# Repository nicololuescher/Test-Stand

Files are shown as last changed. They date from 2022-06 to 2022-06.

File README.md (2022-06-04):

# Modular Test Stand

## What is this?
This is a simple and modular test rig to test hobby rocket motors. It is especially useful to measure homemade rocket motors and check their specs. It is constructed with a modular design in mind. This means that it can simply be converted to measure other forces for other tests.  
I'm neither a Physicist nor a Mechanical Engineer. I'm a Software Engineer. So take this with a grain of salt and feel free to make changes if necesarry.  
  
I just wanted to share my work in hopes that others may find it useful.

## Materials Needed (for my setup)
- ESP32 Microprocessor (NODEESP in my case)
- CZL601 (I have the 50kg version https://www.tinkerforge.com/en/shop/load-cell-50kg-czl601.html)
- HX711 Load Cell Amplifier (https://www.bastelgarage.ch/load-cell-amplifier-hx711-wiegesensor-24-bit)
- Soldering Iron and Jumper Cables
- A USB powerbank
- About 50cm of 20x20mm Aluminium Strut Profile
- 10x M5 T Nut for 20x20mm Strut Profile
- 10x M5x16mm Bolt
- 10x M5 Washer
- 2x M6x30mm Bolt
- 2x M6 Washer
- A 3D Printer
- Basic CAD Knwoledge to create Custom Adapters
- A Server running a MQTT Broker (Mosquitto)

## Prerequisite
You will need a MQTT Broker. [This](https://www.digitalocean.com/community/tutorials/how-to-install-and-secure-the-mosquitto-mqtt-messaging-broker-on-ubuntu-16-04) tutorial from DigitalOcean shows you how you can set up such a service.

## How to build
1. Connect the Load Cell and the Load Cell Amplifier according to the wiring diagram below. (GND - GND, DT - GPIO 16, SCK - GPIO 4, VCC - VCC, Red - E+, Yellow - E-, Black and White - A-, Blue - A+)
wiring

1. Cut 2 pieces from your aluminium extrusion. One about 25cm (lower Structure) and the second about 12cm (upper arm).

1. Print the STL files.

1. Assemble the Scale according to the picture .
scale
esp_container

1. Secure the electronics with cable ties

1. Follow the "Calibrate the Scale" Step in [this](https://randomnerdtutorials.com/esp32-load-cell-hx711/#calibrate-load-cell) tutorial to get the calibration factor

1. Open up the teststand.ino file and fill in your information including the calibration factor in the scale.set_scale(factor). Upload the programm to your ESP32. I recommend you use a mobile hotspot for your wifi connection. This way you are not constrained by your local WIFI.

1. Open up index.html in your Webbrowser of choice (tested in Chrome) and connect your USB Powerbank to the ESP32.

1. Wait until the Scale connectos to the Webinterface.

1. If you see the Connected! prompt in your JS Console and you see data comming in, you are all set.

## How to use the Interface
webinterface
### Enable Graph
This checkbox toggles the Diagram

### Pause / Resume
This button pauses/resumes the datalogging.

### Reset
Clears the ouput. This has no effect on calibration.

### Zero
Zero the scale. E.g. takes the current reading as an offset.

### Tare
To be used in conjunction with Calibrate. Sets the empty weight of the scale. Remove everything on the scale and click "Tare" to start the calibration.

### Calibrate
You have to Tare the scale first. After that, set a known weight on the scale. Put the weight of the object in grams in the input field and click Calibrate. This is useful for when you exchange adapters so you dont have to re-calculate the calibration factor.

### Export Data
This will create a JSON file with all information about the measurement. This includes all variables that are used to calculate the output like zeroOffset and the calibration ratio.

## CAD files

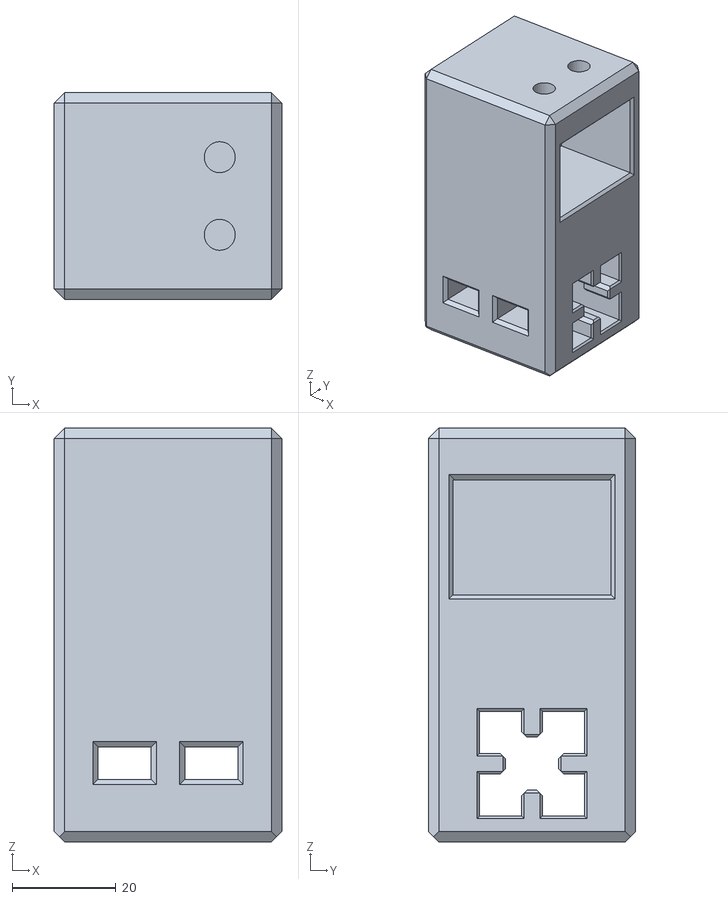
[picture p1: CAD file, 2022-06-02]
Models/upper_connector.stl
44.0 x 40.0 x 80.0

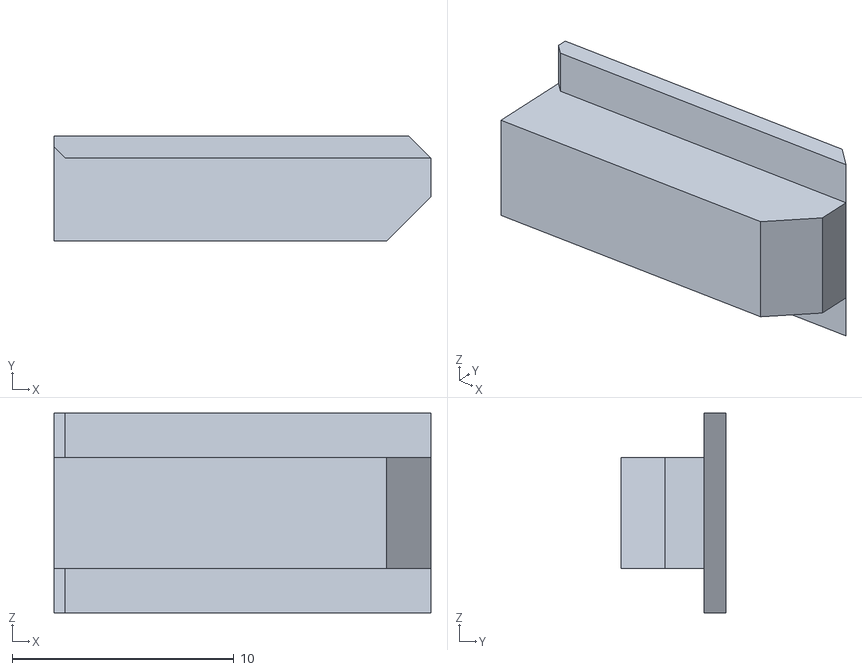
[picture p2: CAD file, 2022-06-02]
Models/lower_connector_key.stl
17.0 x 4.75 x 9.00

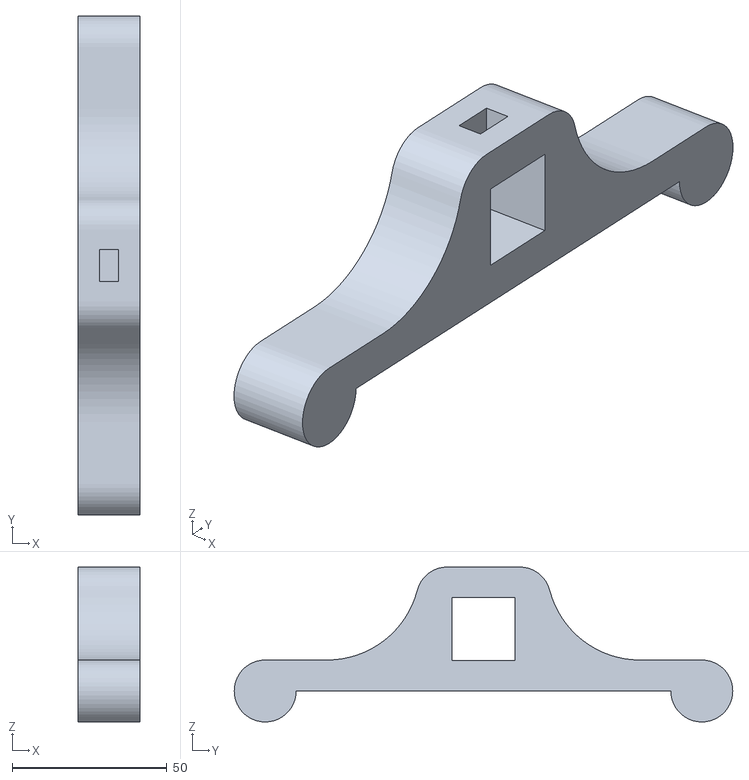
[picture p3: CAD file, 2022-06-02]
Models/foot.stl
20.0 x 160.8 x 50.0

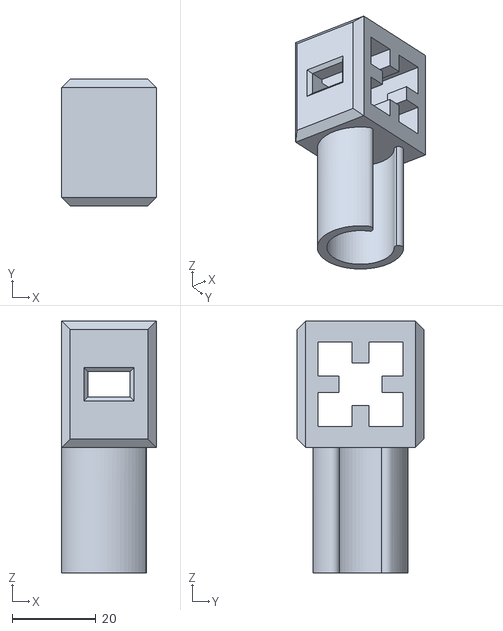
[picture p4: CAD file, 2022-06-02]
Models/adapter_for_17.5mm.stl
22.7 x 30.3 x 60.2

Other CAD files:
Models/lower_connector.stl

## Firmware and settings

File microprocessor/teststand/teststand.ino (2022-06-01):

/*
 * ESP32 Loadcell Test Stand
 * Author: Nicolo Lüscher
 * 2022
 */

#include <Arduino.h>
#include "HX711.h"
#include "soc/rtc.h"
#include <Arduino.h>
#include <WiFi.h>
#include <PubSubClient.h>

const char *SSID = YOUR_SSID;
const char *PWD = YOUR_PASSWORD;

const char *mqttUser = YOUR_MQTT_USER;
const char *mqttPassword = YOUR_MQTT_PASSWORD;

char *mqttServer = YOUR_MQTT_SERVER;
int mqttPort = YOUR_MQTT_PORT;

// HX711 circuit wiring
const int LOADCELL_DOUT_PIN = 16;
const int LOADCELL_SCK_PIN = 4;

char buff[8];

HX711 scale;

WiFiClient wifiClient;

void callback(char *topic, byte *payload, unsigned int length)
{
  // handle message arrived
}

PubSubClient client(mqttServer, mqttPort, callback, wifiClient);

void setupMQTT()
{
  Serial.println("Connecting to MQTT Server");
  if (client.connect("arduinoClient", mqttUser, mqttPassword))
  {
    Serial.println("Connected!");
    client.publish("Status", "ESP Connected!");
  }
  else
  {
    Serial.println("Connection Error!");
  }
}

void connectToWiFi()
{
  Serial.print("Connecting to ");

  WiFi.begin(SSID, PWD);
  Serial.println(SSID);
  while (WiFi.status() != WL_CONNECTED)
  {
    Serial.print(".");
    delay(500);
  }
  Serial.println("Connected.");
}

void setup()
{
  Serial.begin(115200);

  Serial.println("Initializing scale");
  scale.begin(LOADCELL_DOUT_PIN, LOADCELL_SCK_PIN);

  scale.set_scale(91.3);
  scale.tare(); // reset the scale to 0

  Serial.println("Initialization Complete!");
  connectToWiFi();
  setupMQTT();
}

void loop()
{
  dtostrf(scale.get_units(), 6, 2, buff);
  String output = "{\"time\": " + String(millis()) + ", \"data\": " + buff + "}";
  client.publish("reading", output.c_str());
}
